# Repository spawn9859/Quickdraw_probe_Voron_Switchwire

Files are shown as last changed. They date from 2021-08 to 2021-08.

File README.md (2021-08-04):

# Quickdraw probe for Voron Switchwire
A Magnetically Coupled, Removable, Z Probe and Dock System remixed from the files at Annex Engineering so the probe detaches in the X axis on the Voron Switchwire.

Here's a video :
https://www.youtube.com/watch?v=xTww990Z6JU

For the dock arm, dock and probe you will find here, you'll need :
* 6x 6x3mm magnets
* Omron D2F-5 microswitch
* 2x M2x10mm screws
* 2x M5X10mm SHCS
* 2x M5 T-nut for 3030 extrusion

Modified carriage and other infos can be found at Annex Engineering : https://github.com/Annex-Engineering/Quickdraw_Probe

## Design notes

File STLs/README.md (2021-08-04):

The dock is best printed with adaptative layer height or a 0.1mm layer height.

The modified carriage can be found at Annex Engineering here : https://github.com/Annex-Engineering/Quickdraw_Probe/tree/main/XY_Carriages_for_Non-Annex_Printers/VORON_SW/Afterburner%2BMagnetic_Probe_X_Carriage

Do take note that you'll lose 27mm on the X axis for a dock located at X250

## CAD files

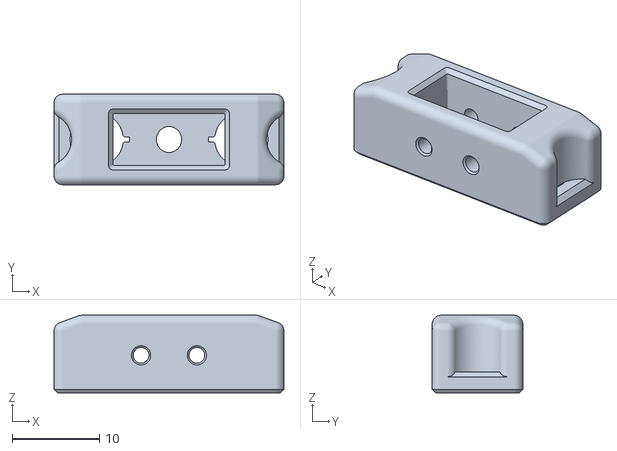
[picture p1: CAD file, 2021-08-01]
STLs/Omron_Mag_Probe_Assembly_remix.stl
26.4 x 10.4 x 8.90

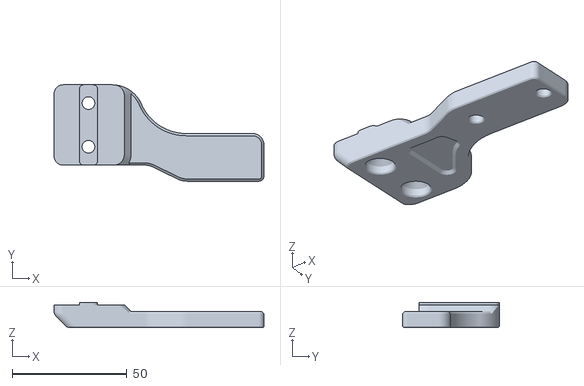
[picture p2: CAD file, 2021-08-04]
STLs/Arm_dock_remix.stl
91.4 x 42.0 x 10.9

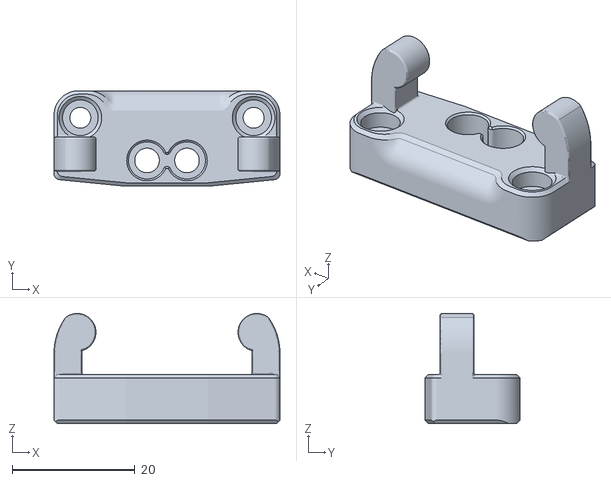
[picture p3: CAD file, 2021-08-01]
STLs/quickdraw_SW_dock_remix.stl
36.8 x 15.5 x 17.9

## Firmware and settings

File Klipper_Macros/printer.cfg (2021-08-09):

[include kiauh_macros.cfg]
[include macros.cfg]
[include start_print_macro.cfg]
[include end_print_macro.cfg]
[include dock_macros.cfg]

[mcu]
serial: /dev/serial/by-id/usb-Klipper_stm32f103xe_32FFD6055359393508780843-if00

[mcu rpi]
serial: /tmp/klipper_host_mcu

[printer]
kinematics: corexz
max_velocity: 250
max_accel: 3200
max_z_velocity: 50
max_z_accel: 1000
square_corner_velocity: 4.0

[stepper_x]
step_pin: PB13
dir_pin: PB12
enable_pin: !PB14
rotation_distance: 40
microsteps: 16
endstop_pin: ^PC0
position_endstop: 250
position_min: 0
position_max: 250
homing_speed: 70
homing_positive_dir: true
homing_retract_dist: 2.5

[tmc2209 stepper_x]
uart_pin: PC11
tx_pin: PC10
uart_address: 0
run_current: 0.5
hold_current: 0.3
interpolate: True
stealthchop_threshold: 1

[stepper_y]
step_pin: PB10
dir_pin: PB2
enable_pin: !PB11
rotation_distance: 40
microsteps: 16
endstop_pin: ^PC1
position_endstop: 232
position_min: -25
position_max: 232
homing_speed: 70
homing_positive_dir: true
homing_retract_dist: 2.5

[tmc2209 stepper_y]
uart_pin: PC11
tx_pin: PC10
uart_address: 2
run_current: 0.5
hold_current: 0.3
interpolate: True
stealthchop_threshold: 1

[stepper_z]
step_pin: PB0
dir_pin: PC5
enable_pin: !PB1
rotation_distance: 40
microsteps: 16
endstop_pin: ^PC2
position_endstop: 251.4625
position_min: -3
position_max: 252
homing_speed: 70
homing_retract_dist: 2.5

[tmc2209 stepper_z]
uart_pin: PC11
tx_pin: PC10
uart_address: 1
run_current: 0.5
hold_current: 0.3
interpolate: True
stealthchop_threshold: 1

[extruder]
max_extrude_only_distance: 150.0
step_pin: PB3
dir_pin: PB4
enable_pin: !PD2
rotation_distance: 7.722
microsteps: 32
nozzle_diameter: 0.400
filament_diameter: 1.750
heater_pin: PC8
pressure_advance_smooth_time: 0.040
sensor_type: ATC Semitec 104GT-2
sensor_pin: PA0
#control = pid
#pid_kp = 18.973
#pid_ki = 0.771
#pid_kd = 116.683
min_temp: 0
max_temp: 270

[tmc2209 extruder]
uart_pin: PC11
tx_pin: PC10
uart_address: 3
run_current: 0.7
hold_current: 0.3
interpolate: True

[probe]
Pin: ^PC14
x_offset: 0.0
y_offset: 34.5
#z_offset: 2.100
speed: 3
samples_result: median
samples_tolerance: 0.05
samples_tolerance_retries: 2

[heater_bed]
heater_pin: PC9
sensor_type: ATC Semitec 104GT-2
sensor_pin: PC3
#control = pid
#pid_kp = 60.695
#pid_ki = 1.073
#pid_kd = 858.069
min_temp: 0
max_temp: 130
pwm_cycle_time: 0.0166

[fan]
pin: PC6

# thermally controlled hotend fan
[heater_fan my_nozzle_fan]
pin: PC7
max_power: 1.0
kick_start_time: 0.100
heater: extruder
heater_temp: 50.0
fan_speed: 1.0

[screws_tilt_adjust]
screw1: 125,84.5
screw1_name: center screw
screw2: 15,-21
screw2_name: front left screw
screw3: 125,-21
screw3_name: front center screw
screw4: 230,-21
screw4_name: front right screw
screw5: 230,84.5
screw5_name: center right screw
screw6: 230,190
screw6_name: rear right screw
screw7: 125,190
screw7_name: rear center screw
screw8: 15,190
screw8_name: rear left screw
screw9: 15,84.5
screw9_name: center left screw
horizontal_move_z: 3
speed: 200
screw_thread: CCW-M3

[bed_mesh]
speed: 150
horizontal_move_z: 3
mesh_min: 15,14.5
mesh_max: 230,225.5
probe_count: 7
relative_reference_index: 12
algorithm: bicubic
fade_start: 1
fade_end: 10
fade_target: 0

[adxl345]
cs_pin: rpi:None

[resonance_tester]
accel_chip: adxl345
probe_points:
    125,119,20  # an example

[input_shaper]
#shaper_freq_x: 51.8
#shaper_type_x: mzv
#shaper_freq_y: 57.6
#shaper_type_y: 2hump_ei

[heater_fan bed_fan]
pin: PA1
max_power: 1.0
kick_start_time: 0.100
heater: extruder
heater_temp: 50.0
fan_speed: 1.0

#[controller_fan my_controller_fan]
#pin: PA1
#max_power: 1.00
#kick_start_time: 0.200
#heater: heater_bed

[static_digital_output usb_pullup_enable]
pins: !PA14

[output_pin LIGHTS]
pin: PC12
value: 0
shutdown_value: 0

[virtual_sdcard]
path: ~/gcode_files

#[gcode_macro lights_on]
#gcode:
 #   SET_PIN PIN=LIGHTS VALUE=1.0

#[gcode_macro lights_off]
#gcode:
#    SET_PIN PIN=LIGHTS VALUE=0.0

[pause_resume]
[firmware_retraction]
[respond]

#*# <---------------------- SAVE_CONFIG ---------------------->
#*# DO NOT EDIT THIS BLOCK OR BELOW. The contents are auto-generated.
#*#
#*# [heater_bed]
#*# control = pid
#*# pid_kp = 60.086
#*# pid_ki = 0.886
#*# pid_kd = 1018.464
#*#
#*# [extruder]
#*# control = pid
#*# pid_kp = 32.245
#*# pid_ki = 1.937
#*# pid_kd = 134.221
#*#
#*# [input_shaper]
#*# shaper_type_x = mzv
#*# shaper_freq_x = 45.8
#*# shaper_type_y = mzv
#*# shaper_freq_y = 56.8
#*#
#*# [probe]
#*# z_offset = 2.275

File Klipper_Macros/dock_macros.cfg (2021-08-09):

###############################################################################
###############################################################################

[gcode_macro GlobalVariables]

# Location of the probe when docked.  
variable_dock_x: 250 # X location
variable_dock_z: 4 # Z location

# What way does the probe detach from the carriage ?
variable_detach: 1 # 1(horizontally/my remix), 2(vertically/Annex)
# What other way can you home the Z-Axis?
variable_initial_homing: 3 # 1(none/probe only), 2(sensorless homing), 3(endstop microswitch)

# The distance to move along x when docking/undocking the probe from the dock
variable_dock_x_offset: 27 # The carriage needs 27mm of clearance with the docked probe
# The distance to move along z when attaching/detaching the probe to/from the toolhead
variable_dock_z_offset: 10
# Travel and Dock speeds
variable_travel_speed: 9000
variable_dock_speed: 6000

# Coordinates of the center of your bed
variable_home_x: 125
variable_home_y: 119
variable_probe_x_offset: 0
variable_probe_y_offset: 34.5

## Sensorless Homing ##
# If you plan to use sensorless homing for the Z axis for the initial homing, enter stepper motors current as in your printer.cfg file
variable_x_run_current: 0.5
variable_x_hold_current: 0.3
variable_z_run_current: 0.5
variable_z_hold_current: 0.3
variable_homing_x_run_current: 0.9 # Those are the values I used with good results for sensorless homing
variable_homing_x_hold_current: 0.9
variable_homing_z_run_current: 0.9
variable_homing_z_hold_current: 0.9

gcode:

###############################################################################
###############################################################################

[homing_override]
axes: xyz
gcode:
    query_probe
    do_Home

[gcode_macro do_Home]
gcode:
    GlobalVariables
    {% set dock_x = printer["gcode_macro GlobalVariables"].dock_x %}
    {% set dock_z = printer["gcode_macro GlobalVariables"].dock_z %}
    {% set detach = printer["gcode_macro GlobalVariables"].detach %}
    {% set dock_z_offset = printer["gcode_macro GlobalVariables"].dock_z_offset %}
    {% set travel_speed = printer["gcode_macro GlobalVariables"].travel_speed %}
    {% set initial_homing = printer["gcode_macro GlobalVariables"].initial_homing %}

    {% if printer.toolhead.homed_axes == 'xyz' %}
        G90
        {% if detach == 1 %}
            G0 Z{ dock_z + dock_z_offset } F{ travel_speed }
        {% endif %}
        {% if detach == 2 %}
            G0 Z{ dock_z } F{ travel_speed }
        {% endif %}

        G28 X0 Y0
        
        Attach_probe
        PROBE_HOMING

	{% else %}
        SET_KINEMATIC_POSITION X={ dock_x } Z=0
        G90
        {% if detach == 1 %}
            G0 Z{ dock_z + dock_z_offset } F{ travel_speed }
        {% endif %}
        {% if detach == 2 %}
            G0 Z{ dock_z } F{ travel_speed }
        {% endif %}

        G28 X0 Y0

        {% if printer.probe.last_query == 0 %}
            PROBE_HOMING
        {% endif %}

        {% if printer.probe.last_query == 1 %}
            {% if initial_homing == 1 %}
                RESPOND TYPE=error MSG="Please attach probe"
                M117 Please attach probe
            {% endif %}
           {% if initial_homing == 2 %}
                SENSORLESS_HOMING
            {% endif %}
            {% if initial_homing == 3 %}
                PROBELESS_HOMING
            {% endif %}
        {% endif %}
    {% endif %}

[gcode_macro PROBELESS_HOMING]
gcode:
    GlobalVariables
    {% set dock_z = printer["gcode_macro GlobalVariables"].dock_z %}
    {% set dock_z_offset = printer["gcode_macro GlobalVariables"].dock_z_offset %}
    {% set travel_speed = printer["gcode_macro GlobalVariables"].travel_speed %}
    {% set home_x = printer["gcode_macro GlobalVariables"].home_x %}
    {% set home_y = printer["gcode_macro GlobalVariables"].home_y %}
    {% set probe_x_offset = printer["gcode_macro GlobalVariables"].probe_x_offset %}
    {% set probe_y_offset = printer["gcode_macro GlobalVariables"].probe_y_offset %}
    
    G0 X{ home_x - probe_x_offset } Y{ home_y - probe_y_offset } F{ travel_speed }
    G28 Z0
    G0 Z{dock_z + dock_z_offset } F{ travel_speed }
    Attach_probe
    Adjust_Z

[gcode_macro Set_Home_Current]
gcode:
    GlobalVariables
    {% set homing_x_run_current = printer["gcode_macro GlobalVariables"].homing_x_run_current %}
    {% set homing_x_hold_current = printer["gcode_macro GlobalVariables"].homing_x_hold_current %}
    {% set homing_z_run_current = printer["gcode_macro GlobalVariables"].homing_z_run_current %}
    {% set homing_z_hold_current = printer["gcode_macro GlobalVariables"].homing_z_hold_current %}

    SET_TMC_CURRENT STEPPER=stepper_x CURRENT=homing_x_run_current HOLDCURRENT=homing_x_run_current
    SET_TMC_CURRENT STEPPER=stepper_z CURRENT=homing_x_run_current HOLDCURRENT=homing_x_run_current

[gcode_macro Set_Print_Current]
gcode:
    GlobalVariables
    {% set x_run_current = printer["gcode_macro GlobalVariables"].x_run_current %}
    {% set x_hold_current = printer["gcode_macro GlobalVariables"].x_hold_current %}
    {% set z_run_current = printer["gcode_macro GlobalVariables"].z_run_current %}
    {% set z_hold_current = printer["gcode_macro GlobalVariables"].z_hold_current %}

    SET_TMC_CURRENT STEPPER=stepper_x CURRENT={ x_run_current } HOLDCURRENT={ x_hold_current }
    SET_TMC_CURRENT STEPPER=stepper_z CURRENT={ z_run_current } HOLDCURRENT={ z_hold_current }

[gcode_macro SENSORLESS_HOMING]
gcode:
    GlobalVariables
    {% set dock_z = printer["gcode_macro GlobalVariables"].dock_z %}
    {% set dock_z_offset = printer["gcode_macro GlobalVariables"].dock_z_offset %}
    {% set travel_speed = printer["gcode_macro GlobalVariables"].travel_speed %}
    {% set home_x = printer["gcode_macro GlobalVariables"].home_x %}
    {% set probe_x_offset = printer["gcode_macro GlobalVariables"].probe_x_offset %}

    G0 X{ home_x - probe_x_offset } Y-21 F9000
    Set_Home_Current
    G28 Z0
    G0 Z{dock_z + dock_z_offset } F{ travel_speed }
    Set_Print_Current
    G28 X0
    Attach_probe
    Adjust_Z

[gcode_macro PROBE_HOMING]
gcode:
    Adjust_Z

[gcode_macro Adjust_Z]
gcode:
    GlobalVariables
    {% set travel_speed = printer["gcode_macro GlobalVariables"].travel_speed %}
    {% set home_x = printer["gcode_macro GlobalVariables"].home_x %}
    {% set home_y = printer["gcode_macro GlobalVariables"].home_y %}
    {% set probe_x_offset = printer["gcode_macro GlobalVariables"].probe_x_offset %}
    {% set probe_y_offset = printer["gcode_macro GlobalVariables"].probe_y_offset %}
    {% set probe_offset_z = printer.configfile.config.probe.z_offset|float %}

    G0 X{ home_x - probe_x_offset } Y{ home_y - probe_y_offset } F { travel_speed }
    SET_KINEMATIC_POSITION Z=250
    PROBE PROBE_SPEED=10
    G91
    G0 Z2 F{ travel_speed }
    G90
    PROBE samples=3 SAMPLE_RETRACT_DIST=1
    SET_KINEMATIC_POSITION Z={probe_offset_z}
    G0 Z4 F{ travel_speed }

[gcode_macro Dock_probe]
gcode:
    query_probe
    do_Dock

[gcode_macro do_Dock]
gcode:
    {% if printer.probe.last_query == 1 %}
        RESPOND PREFIX= MSG="Probe is already docked!"
        M117 Probe is already docked!

    {% else %}
	    GlobalVariables
        {% set dock_x = printer["gcode_macro GlobalVariables"].dock_x %}
        {% set dock_z = printer["gcode_macro GlobalVariables"].dock_z %}
        {% set detach = printer["gcode_macro GlobalVariables"].detach %}
        {% set home_y = printer["gcode_macro GlobalVariables"].home_y %}
        {% set dock_x_offset = printer["gcode_macro GlobalVariables"].dock_x_offset %}
        {% set dock_z_offset = printer["gcode_macro GlobalVariables"].dock_z_offset %}
        {% set travel_speed = printer["gcode_macro GlobalVariables"].travel_speed %}
        {% set dock_speed = printer["gcode_macro GlobalVariables"].dock_speed %}
        {% set probe_y_offset = printer["gcode_macro GlobalVariables"].probe_y_offset %}

        {% if printer.toolhead.homed_axes != 'xyz' %}
	        G28	# Home All Axes
	    {% endif %}

        G90
        {% if detach == 1 %}
            G0 Z{ dock_z + dock_z_offset } F{ travel_speed }
        {% endif %}
        {% if detach == 2 %}
            G0 X{ dock_x - dock_x_offset } F{ travel_speed }
            G0 Z{ dock_z } F{ travel_speed }
        {% endif %}
        G0 X{ dock_x } Y{ home_y - probe_y_offset } F{ dock_speed }
        {% if detach == 1 %}
            G0 Z{ dock_z } F{ dock_speed }
        {% endif %}
        {% if detach == 2 %}
            G0 Z{ dock_z + dock_z_offset } F{ dock_speed }
        {% endif %}
        G0 X{ dock_x - dock_x_offset } Y{ home_y - probe_y_offset } F{ dock_speed }
        G0 Z5 F{ travel_speed }
    {% endif %}

    verify_Docking

[gcode_macro verify_Docking]
gcode:
    query_probe
    safe_Dock

[gcode_macro safe_Dock]
gcode:
    {% if printer.probe.last_query != 1 %}
        M112
    {% endif %}
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

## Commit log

2021-08-02 Add files via upload
    Add sensorless homing to attach probe if it is not already attached
    [dock_macros.cfg]
2021-08-04 Add files via upload
    Add options for sensorless homing, endstop homing and probe-only homing
    [dock_macros.cfg]
2021-08-04 Code cleaning
    [dock_macros.cfg]
2021-08-04 Added remixed dock arm
    I remixed the dock arm to shave off 3mm in thickness, saving 3mm in X build space. M5 holes are more spaced, alloweing for better clearance for M5 T-nuts allowing them to rotate and lock better.
    [Arm_dock_remix.stl]
2021-08-04 Changed values for remixed dock arm
    [dock_macros.cfg]
2021-08-04 Code cleaning, added comment on dock_x_offset
    [dock_macros.cfg]
2021-08-04 Code cleaning, added bed_mesh_calibrate macro
    [dock_macros.cfg]
2021-08-05 Added some probe macro renames in order to attach probe before hand, better homing if toolhead position is already known
    [dock_macros.cfg]
2021-08-06 Code cleaning, added options for sensorless homing run and hold current in configurator
    [dock_macros.cfg, kiauh_macros.cfg, macros.cfg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]
2021-08-09 Faster first probing, slower subsequent probing
    [dock_macros.cfg, printer.cfg]
